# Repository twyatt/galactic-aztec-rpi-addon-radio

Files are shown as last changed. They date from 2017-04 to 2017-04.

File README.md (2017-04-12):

# About
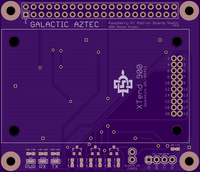
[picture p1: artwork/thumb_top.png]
OSHPark PCB Top Thumbnail

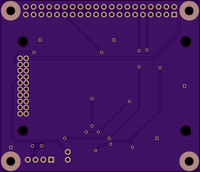
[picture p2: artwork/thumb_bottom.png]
OSHPark PCB Bottom Thumbnail


Custom Raspberry Pi Add-on board used during the launch of the [Galactic Aztec] rocket to transmit telemetry data. The board was designed to be stackable with other add-on boards via the designated [pin configuration].

Custom EagleCAD parts on this board can be found in the [SDSU Rocket Eagle Libraries].

# Bill of Materials
| Qty | Description | Part Number | Vendor |
|:---:|---|---:|---|
| 1 | LED Green Vf=1.7V If=2mA 0603 | [475-1193-1-ND] | DigiKey |
| 1 | LED Red Vf=1.8V If=2mA 0603 | [475-1195-2-ND] | DigiKey |
| 1 | LED Yellow Vf=1.8V If=2mA 0603 | [475-1196-1-ND] | DigiKey |
| 3 | MOSFET N-Channel 50V 220mA SOT-23 | [BSS138CT-ND] | DigiKey |
| 2 | Resistor 1.8kΩ 1/4W 1% 0603 | [P1.8KBYCT-ND] | DigiKey |
| 7 | Resistor 10kΩ 1/4W 1% 0603 | [P10KBYCT-ND] | DigiKey |
| 1 | Resistor 820Ω 1/4W 1% 0603 | [P820BYCT-ND] | DigiKey |
| 1 | Header 2x10 2mm Pitch | [S5750-10-ND] | DigiKey |
| 1 | Header Female 1x4 0.1" Pitch | [S7037-ND] | DigiKey |
| 1 | Header Stacking 2x20 Tall 23mm | [1979] | Adafruit |
| 1 | 100 ct. No. 4 Nylon Spacer 3/16" OD 1/4" Length | [94639A706] | McMaster-Carr |
| 1 | 100 ct. 18-8 Stainless Steel Screw 4-40 7/16" | [91772A109] | McMaster-Carr |
| 1 | XTend 900 900Mhz 1W | [XT09-SI-ND] | DigiKey |

[Galactic Aztec]: http://rocket.sdsu.edu/rockets
[pin configuration]: https://docs.google.com/spreadsheets/d/1zGslKhH-ZteeA8sbbTjQlF-Neb-wJ3quIlFH6I8Cvgs/edit?usp=sharing
[SDSU Rocket Eagle Libraries]: https://github.com/twyatt/SDSURocket-Eagle-Libraries
[475-1193-1-ND]: http://www.digikey.com/product-detail/en/LG%20L29K-F2J1-24/475-1193-1-ND/810354
[475-1195-2-ND]: http://www.digikey.com/product-detail/en/LS%20L29K-H1J2-1-Z/475-1195-1-ND/810356
[475-1196-1-ND]: http://www.digikey.com/product-detail/en/LY%20L29K-H1K2-26-Z/475-1196-1-ND/810357
[BSS138CT-ND]: http://www.digikey.com/product-detail/en/BSS138/BSS138CT-ND/244294
[P1.8KBYCT-ND]: http://www.digikey.com/product-detail/en/ERJ-PA3F1801V/P1.8KBYCT-ND/5036145
[P10KBYCT-ND]: http://www.digikey.com/product-detail/en/ERJ-PA3F1002V/P10KBYCT-ND/5036115
[P820BYCT-ND]: http://www.digikey.com/product-detail/en/ERJ-PA3F8200V/P820BYCT-ND/5036224
[S5750-10-ND]: http://www.digikey.com/product-detail/en/NPPN102AFCN-RC/S5750-10-ND/804795
[S7037-ND]: http://www.digikey.com/product-detail/en/PPPC041LFBN-RC/S7037-ND/810176
[1979]: http://www.adafruit.com/products/1979
[94639A706]: http://www.mcmaster.com/#94639a620/=weyw3h
[91772A109]: http://www.mcmaster.com/#91772a109/=wau506
[XT09-SI-ND]: http://www.digikey.com/product-detail/en/XT09-SI/XT09-SI-ND/688312

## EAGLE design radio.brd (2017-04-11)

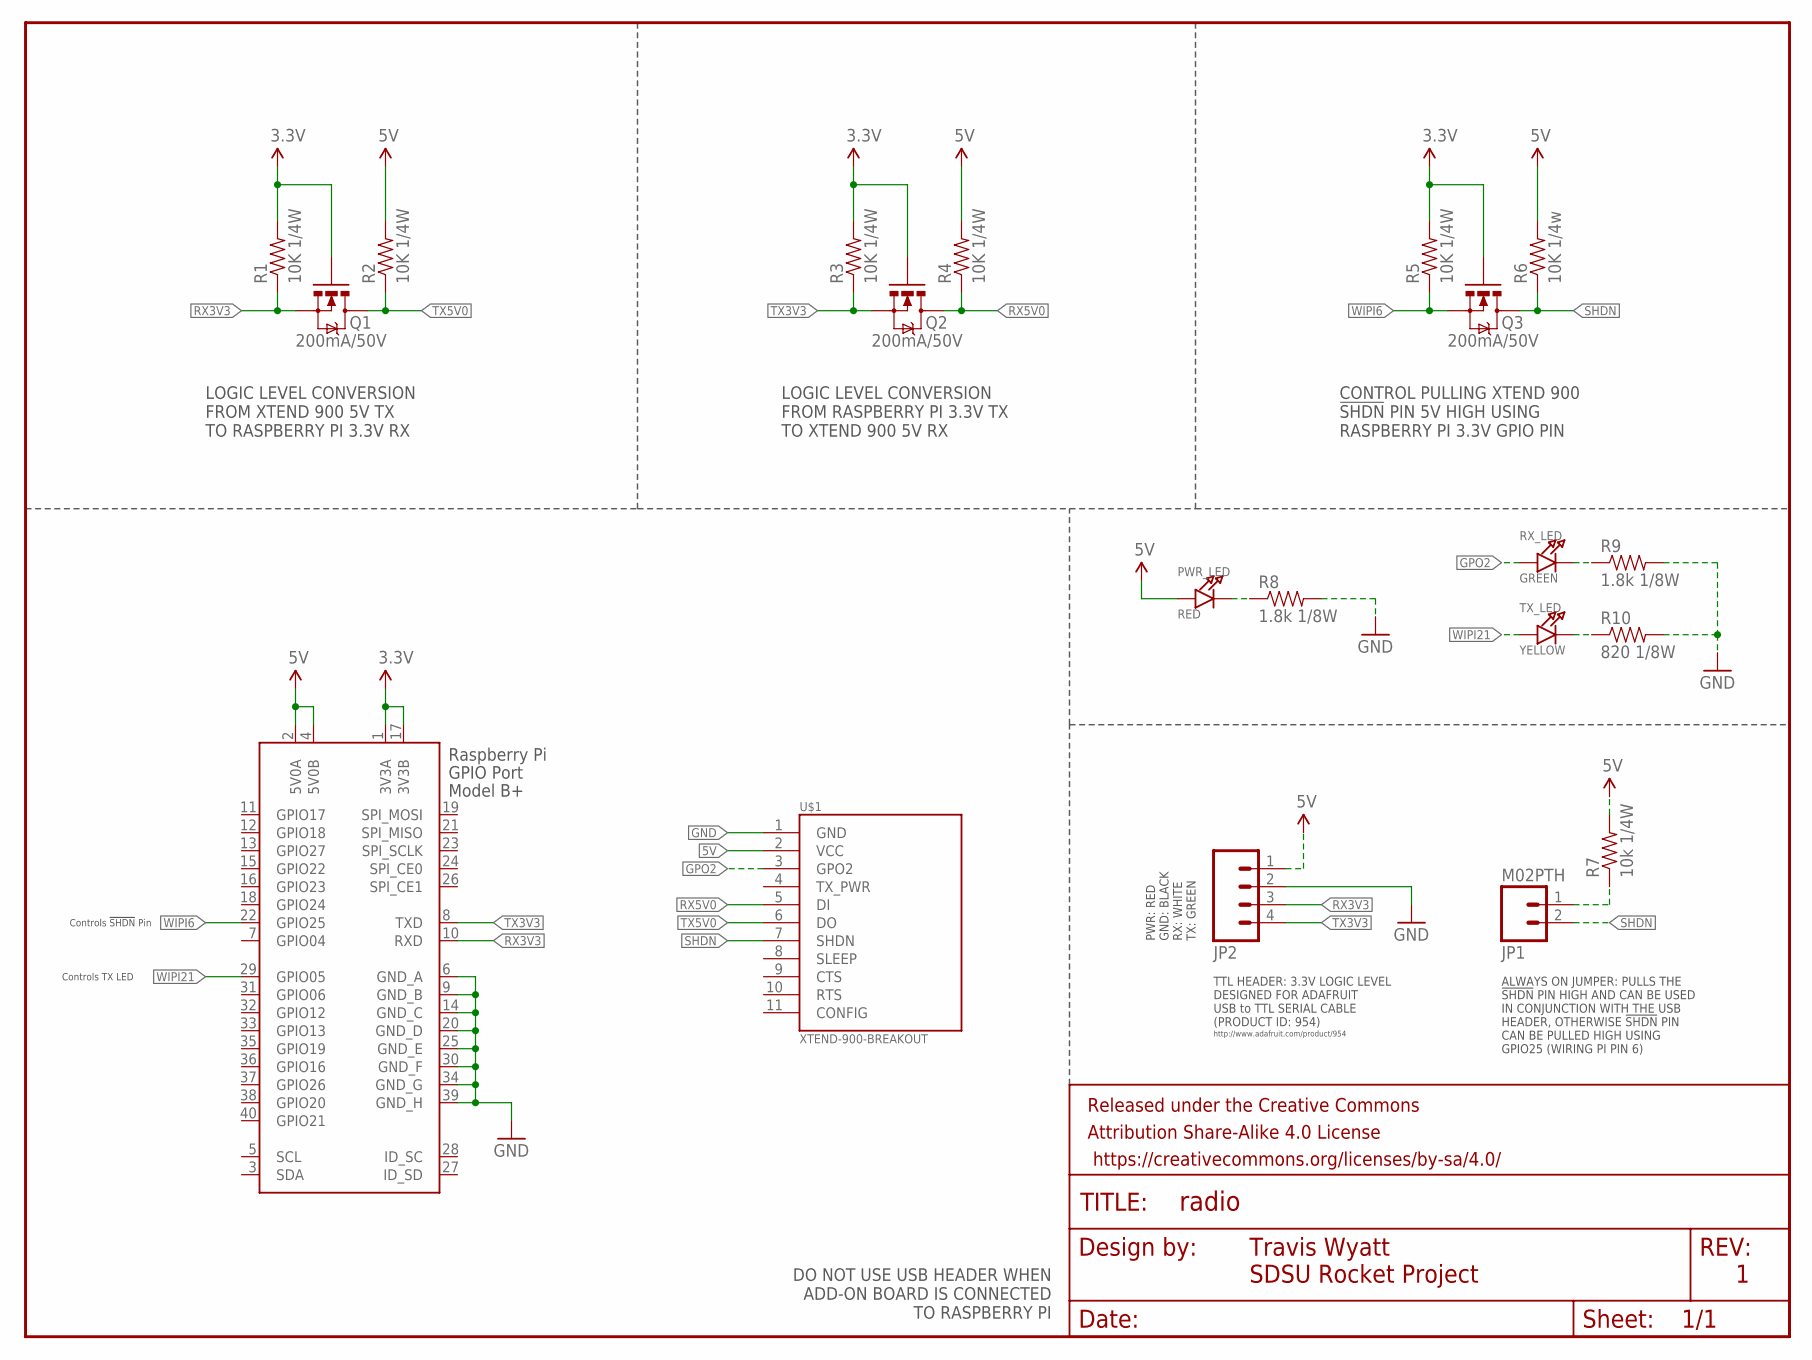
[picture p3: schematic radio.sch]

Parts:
FRAME1: FRAME-LETTER; CREATIVE_COMMONS
JP1: M02PTH; 1X02
JP2: M04PTH; 1X04
PWR_LED: RED; CHIPLED_0603
Q1, Q2, Q3: 200mA/50V; SOT23-3
R1, R2, R3, R4, R5: 10K 1/4W; 0603-RES
R6: 10K 1/4w; 0603-RES
R7: 10k 1/4W; 0603-RES
R8, R9: 1.8k 1/8W; 0603-RES
R10: 820 1/8W; 0603-RES
RX_LED: GREEN; CHIPLED_0603
TX_LED: YELLOW; CHIPLED_0603
U$1: XTEND-900-BREAKOUT; XTEND-900
X1: RASPI_BOARD_B+#_H; RASPI_BOARD_B+HAT

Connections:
3.3V: Q1.1 (G), Q2.1 (G), Q3.1 (G), R1.2, R3.2, R5.2, X1.1 (3V3A), X1.17 (3V3B)
5V: JP2.1, PWR_LED.A, R2.2, R4.2, R6.2, R7.2, U$1.2 (VCC), X1.2 (5V0A), X1.4 (5V0B)
GND: JP2.2, R8.2, R9.2, R10.2, U$1.1 (GND), X1.6 (GND_A), X1.9 (GND_B), X1.14 (GND_C), X1.20 (GND_D), X1.25 (GND_E), X1.30 (GND_F), X1.34 (GND_G), X1.39 (GND_H)
GPO2: RX_LED.A, U$1.3 (GPO2)
unnamed: JP1.1, R7.1
unnamed: PWR_LED.C, R8.1
unnamed: R9.1, RX_LED.C
unnamed: R10.1, TX_LED.C
RX3V3: JP2.3, Q1.2 (S), R1.1, X1.10 (RXD)
RX5V0: Q2.3 (D), R4.1, U$1.5 (DI)
SHDN: JP1.2, Q3.3 (D), R6.1, U$1.7 (SHDN)
TX3V3: JP2.4, Q2.2 (S), R3.1, X1.8 (TXD)
TX5V0: Q1.3 (D), R2.1, U$1.6 (DO)
WIPI6: Q3.2 (S), R5.1, X1.22 (GPIO25)
WIPI21: TX_LED.A, X1.29 (GPIO05)

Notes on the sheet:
Travis Wyatt
SDSU Rocket Project
Controls !SHDN! Pin
LOGIC LEVEL CONVERSION FROM RASPBERRY PI 3.3V TX TO XTEND 900 5V RX
LOGIC LEVEL CONVERSION FROM XTEND 900 5V TX TO RASPBERRY PI 3.3V RX
CONTROL PULLING XTEND 900 !SHDN! PIN 5V HIGH USING RASPBERRY PI 3.3V GPIO PIN
PWR: RED GND: BLACK RX: WHITE TX: GREEN
ALWAYS ON JUMPER: PULLS THE !SHDN! PIN HIGH AND CAN BE USED IN CONJUNCTION WITH THE USB HEADER, OTHERWISE !SHDN! PIN CAN BE PULLED HIGH USING GPIO25 (WIRING PI PIN 6)
TTL HEADER: 3.3V LOGIC LEVEL DESIGNED FOR ADAFRUIT USB to TTL SERIAL CABLE (PRODUCT ID: 954)
DO NOT USE USB HEADER WHEN ADD-ON BOARD IS CONNECTED TO RASPBERRY PI
http://www.adafruit.com/product/954
Controls TX LED

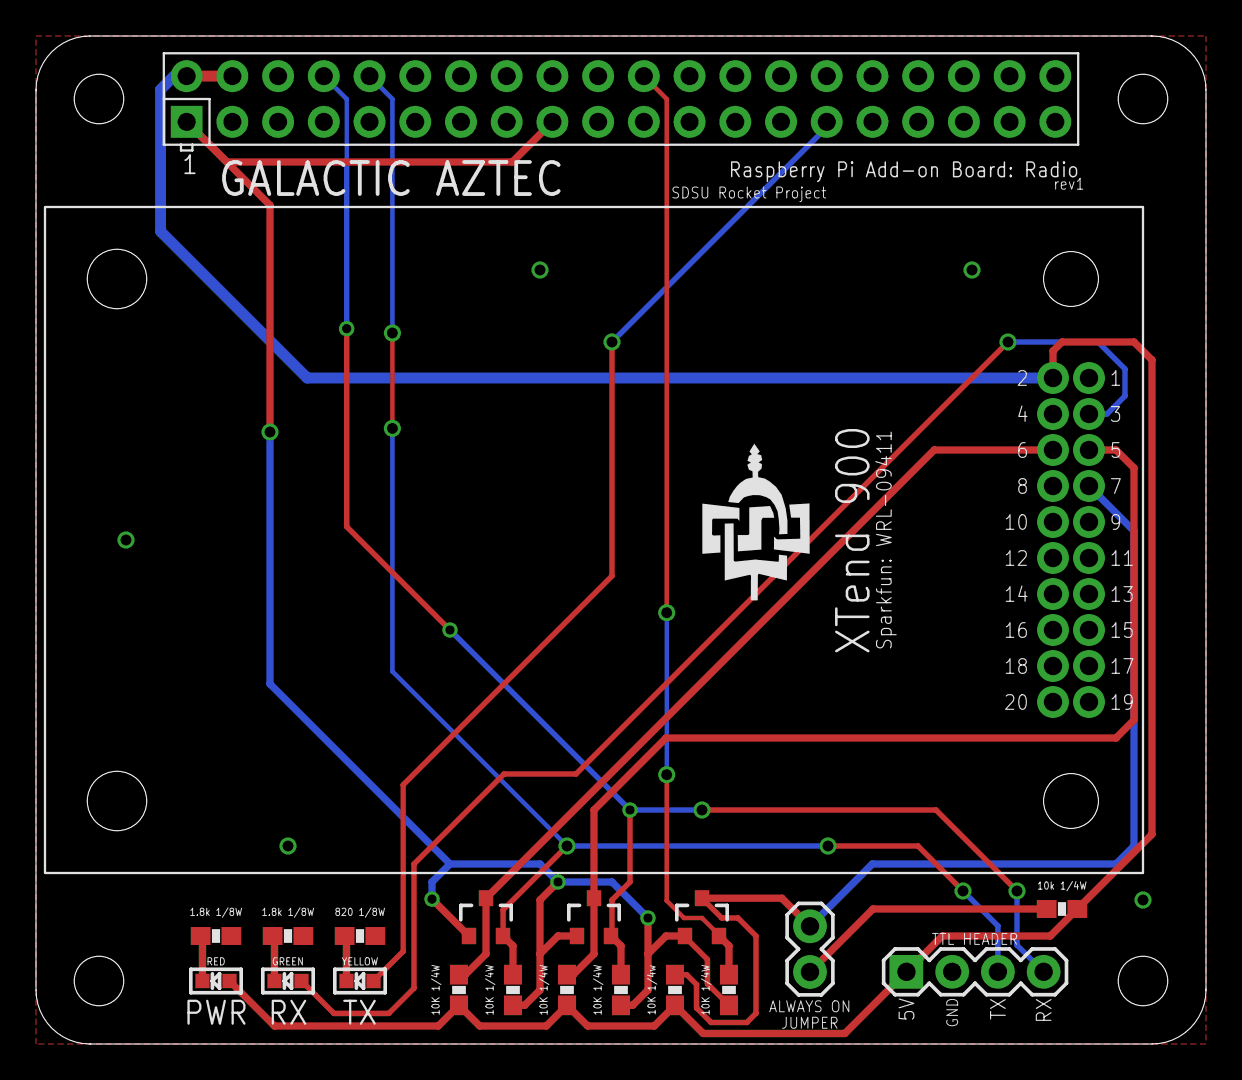
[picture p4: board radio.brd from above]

Board: 2 copper layers, 65.0 x 56.0 mm, 21 parts (0 on the bottom side), 15 nets.

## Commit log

2017-04-11 Add schematic/board design and artwork
    [radio.brd, radio.sch]
2017-04-12 Add README with brief description and BOM

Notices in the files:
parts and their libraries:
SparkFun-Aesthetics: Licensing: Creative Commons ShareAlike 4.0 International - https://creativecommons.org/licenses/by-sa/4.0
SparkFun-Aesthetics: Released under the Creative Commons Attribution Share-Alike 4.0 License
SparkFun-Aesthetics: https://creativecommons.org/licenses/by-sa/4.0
